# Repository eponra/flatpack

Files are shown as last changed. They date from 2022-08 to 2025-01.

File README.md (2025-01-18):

# flatpack
There is not a lot to unpack. Like... for real.

https://user-images.githubusercontent.com/66600478/183345870-d31b0fc4-497d-4f51-bbe5-db83cf9a2b46.mp4

https://user-images.githubusercontent.com/66600478/183403170-353edabf-4271-400f-9db7-fafc17dc54a0.mp4

https://user-images.githubusercontent.com/66600478/183500945-2cf039b2-9133-45dd-af40-6a08152f20f8.mp4

(flatpack and flathead printing gridfinity parts; flatpack with the old hotendsetup (4010 hotend, 3010 for partcooling)

###### Small Announcement before we go on here:

Mellow has made a fully machined adaptation of flatpack, this machine is called the Mellow M1. Apart from still being able to be folded,
it comes with:
- a new board which is basically a Fly D5 and a Fly Pi Lite v2 married together on the size of the D5 (im very much looking forward
to that board, apart from the cnc'ed adaption of my design is running Flipper ofc; they could do rrf, but we will see)
- a 2.8" touchscreen at the bottom, and a 1.3" touchscreen at the hotend for quick filament changes and quick heating
- a fully cnc'ed frame

- here is the shoplink (no affiliation): https://a.aliexpress.com/_EHAE37a
- There was the idea of doing a kickstarter as every company right now is doing, but mellow ultimately decided against it

https://youtu.be/e8mjv9e-qzc (you see two prototypes here at TCT Asia)  
https://youtu.be/q5g9Ud7NPts?si=8peJaGWEXCFL_qLP&t=52 (starting at the timestamp you see one prototype again)  

Im in no way affiliated with mellow, i dont get anything out of this EXCEPT one of the finished mellow m1. Which im looking very much forward too.

And now lets go on with flatpack here:

###### Technical Data:

- folded volume of roughly 220x210x75mm (so, make sure your spoolbox has these
  inner dimensions at a minimum, as there are some with slightly different dimensions)
- buildvolume of 120x114x114mm, so 1.6 liters
- heated bed that can reach up to 110°C
- Hotend capable of temperatures up to 300°C, if you choose the Copper NF Smart 500°C
- powered through an external (!) powerbrick with 150W, uses 100W max
- the design can theoretically use an AC bed, and consequently a small psu
  enabling everything to fit in one box. 
  For safety reasons I deemed mains wiring to be to dangerous and
  as a result I have selected a DC powered bed to make the build more accessible to the average user.
- Flatpack is fully reprap, meaning that you can print every printable part of flatpack on flatpack.
- now also with Klipper or Octoprint! You need at least the Pi Zero Mount from the files for adding that.
You have also the possibility now to drop the AIO II and just install an SKR Pico along with an Pi Zero (2) W

###### Firmware:

- Marlin configuration is available at [firmware/Marlin](firmware/Marlin). Tested with the AIO II.

###### Some words of caution:

- As you can imagine, a fixed bed cantilever is not optimal for fast speeds or
  larger printvolumes.
- Thankfully, we dont have to deal with a large printvolume. Speed and Acceleration are however a concern here.
Rapid changes in direction can be challenging for any motion system and even more so with this motion system.
As a result consider setting your print speeds and accelerations conservatively.
- So why the fixed bed cantilever? Because it simply looks cool.
- Dual rails are used for load distribution on both the Y and Z axis; these can be a bit
  tricky to align, and can and will cost you a few grey hairs.
- last word of caution: I encourage you to take your time building flatpack, and make certain everything is square, and all the motion system moves smoothly, while everything that should not move is rigid and secure without much play or flexing. 
- its a (functioning) prototype, and will continue to undergo active development and improvements.
- thanks to the user awesomeka001 we now know, that the xz-joiner is indeed printable on flatpack, so flatpack is now full reprap. Meaning if you have one flatpack, you can print all parts of it on that machine.

## This is free for everyone to download and build, or of course to just look at it and take some inspiration or ideas from it. :)

###### ToDo-List
- the XY-joiner is realtively complicated to print and cleanup. One day ill find an easier way to do that.
- flatpack has no spoolholder. The goal is to design a spoolholder, that can travel along in the spoolbox along side the filament you´re carrying with you
- we now have an adapter to fit a Mellow Orbiter Extruder. One day i will make a new carriage for that, so we dont need an adapter, but for now the adapter works well enough, and its still foldable.
- Further optimization of the fanduct/part cooling. I have encountered difficulties designing the fanduct. I have started a repo for ["caterpillar"](https://www.github.com/eponra/caterpillar), which is a partcoolingsolution I designed using CF tubes, which I intend to merge into flatpack eventually.
- the current 3 point-bedmounting is not optimal, as it is simply drilled and tapped M3 threaded holes. I would like to find a better solution down the road.
- you can twist the base and that's not supposed to happen! One solution is to drill through the aluminium extrusions to get screws into the extrusions under the bed. I am convinced there is probably a better solution.

prototyping
(for a break, the latest switch from a totally different hotend/partcooling setup to the actual one. Thats not all steps, just a few)

## Design files

[Fusion 360 Web Flatpack](https://a360.co/3vLUHdm)

This link is sadly viewable only, as I am using the free version of Autodesk
Fusion 360. I also put up a version that only shows parts and positions of the heated inserts. (Attention: the parts inside this are not the most recent, so dont print these.)

[Fusion 360 Web heated inserts](https://a360.co/3tjAQnn)

The link to the latest stable .step file (Ver7) is [here](https://drive.google.com/file/d/1WWorgIL0F1IlGSLJlwn24FICozzornDs/view)
The link to the latest stable Fusion360 file (Ver7) is [here](https://drive.google.com/file/d/1Mac7FewMhGuZk7lCGxoMbQp6idila8Fw/view?usp=drive_link)

###### Changelog:
- from V6 to V7 where changes made to the XZ-joiner, the left Frontmount (so that we can use a shorter front extrusion, this lets us use only 4 300mm 1515 extrusions), i added the screwingholes to the drawing so you know where
to add the extra screws for the base, i added a component which only includes all parts that have inserts + the heated inserts (in a slightly exploded configuration, so you can better see where every insert needs to be), slightly changed
X-Tensioner (just to make one M3-head flush with the print)
- from V4 to V6 there are changes in the X and Y tensioner. Both clamps now feature copper pressfit bushings, and M3 rods. If you started printing already, you only have to watch out for "Y-Tensioner Clamp long v2" and "X-Tensioner Clamp v2".

This is the SKR Pico in front, with the Pi Zero (2) W mount underneath the bed. This is for either Klipper or Octoprint (for Octoprint you can use the AIO II plus the Pi Zero (2) W, and dont need the BTT SKR Pico)


###### A few words of gratitude:

The initial idea of a fixed bed cantilever was not mine, but came from
[apsu](https://github.com/apsu), a constant resident of the
#reprap-and-custombuilds channel in the [3D Printing
discord](https://discord.gg/pQRvDQHk67).  With this i built flathead, the
bigger brother of flatpack, and without [apsu](https://github.com/apsu/) none
of this would have happened.

The initial idea to make this foldable, came from @Ogre.

Also, special thanks to [oliof](https://github.com/oliof/), another extremely
helpful member and Mod of 3D printing, and also a walking dictionary on obscure
3D printing and mechanical knowledge.  And of course, a thank you to everyone
else i forgot from 3D printing and especially the #reprap-and-custombuilds
channel.

Also, everyone nagging me multiple times a day in the super secret
#wheres-flatpack channel...

Flatpack is licensed under [GPL v3.0](/LICENSE).

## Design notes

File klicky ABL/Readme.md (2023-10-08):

## Klicky On Flatpack

#### NOTES
- Since the Z on this printer moves, if you power off the printer at anywhere but Z0, the hotend wont be able to grab the probe  
as it uses it to home Z I havent found a solution yet so let me know if you have any ideas  
- You lose a tiny bit of build volume  

### 1. Printed Parts
 - You need 3 parts for this
 - The **duct**, the standard **probe holder**, and the **probe dock**
 - All 3 parts should be printed in asa or abs as they are near the hotend and bed  
  
    **Duct:**
    - The duct has 3 holes for magnets which you need to press wires into, just the 2 connected to the switch,  
and then you need to trim a hole in the duct for the wires to run out past the fan  
    - Then, you need to run the wires back to the motherboard using the cable sleeving  
    - The duct just mounts like normal with 2 M3 Screws  
    
    **Probe Holder:**
    - The probe holder is just the standard Klicky probe holder 
    - You screw the limit switch in and attach the 3 top magnets 
    - Do not attach the one on the side as its not needed because the probe docks backwards
    
    **Probe Dock:**
    - The probe dock uses 1 magnet and 2 m3 screws
    - It mounts on the 1515 extrusion that has the top y linear rail on it beside the bed
    - It is at X2 Y114 or Y0 (Depending on your setup) roughly
    
### 2. BOM
 What you will need:
 - 4 6x3 Magnets
 - 1 Omron D2F-5
 - 2 STEEL M2 Screws (They need to stick to the dock magnet as the probe is backwards)
 - Wire
 - Super Glue (If necessary)
 - 2 M3x8 Screws 
 - 2 M3 Nuts
 - 1 Heated Insert for Duct
 
 ### 3. Assembly
  - Assemble the Klicky probe by putting the 3 magnets in the top and screwing the limit switch in
  - Insert the 3 Magnets into the duct along with 2 wires on the left and right magnets so the switch can work (I recommend testing continuity with them)
  - Trim a small hole in the end of the duct to allow the wires to come out, on the right side of the fan
  - Route the wires to the motherboard and attach them to z stop or a probe pin (I use z stop)
  - Attach the one magnet into the probe dock and use the 2 M3 screws and nuts to attach it to the 1515 extrusion that is where the y belt tensioner is
  - Move flatpack manually until you find the coordinates of the klicky probe, Mark them down (For me they are Z12.62 Y6 X2)
  **Thats It!! Assembly for Klicky is done**
  
  ### 4. Firmware
Instructions based on Marlin 2.1.2.1
    If you are using Klipper, there are guides online  
    Used this as a reference https://www.youtube.com/watch?v=egWpvaTsl10  
    ### - **Configuration.h**  
          - Uncomment #define Z_MIN_PROBE_USES_Z_MIN_ENDSTOP_PIN  
          - Uncomment #define FIX_MOUNTED_PROBE  
          - Uncomment #define NOZZLE_TO_PROBE_OFFSET { 21.4, -11.4, -10.75} (Those are my offset values in order of XYZ)  
          - Set #define PROBING_MARGIN to 15  
          - Set #define Z_CLEARANCE_DEPLOY_PROBE 0 and #define Z_CLEARANCE_BETWEEN_PROBES 5  
          - Make sure #define Z_PROBE_LOW_POINT is set to -5   
          - Uncomment #define RESTORE_LEVELING_AFTER_G28  
          - Uncomment #define LCD_BED_LEVELING  
          - Uncomment #define Z_SAFE_HOMING  
          - Uncomment #define AUTO_BED_LEVELING_BILINEAR  
          - If you want, you can uncomment this to test your mesh #define G26_MESH_VALIDATION  
          - Set  #define GRID_MAX_POINTS_X to 5  
    ### - **Configuration_adv.h**  
          - These are all your macros for abl, you may have to change the values depending on where your mount is  

#### Here are my custom macros:   

> ; Macros
> ; M810 Home XY  and deploy probe
> M810 G28 XY|G1 Z12.62|G1 X2|G1 Y11 F2400|G1 X2 Y6 Z12.62 F1200|G1 Y25 Z12.62 F2400
>
> ; M811 Home XYZ and stow probe
> M811 G28 XYZ|G1 Z12.62|G1 X2|G1 Y11 F2400|G1 X2 Y6 Z12.62 F1200|G1 X50 Y6 Z12.62 F2400
> 
> ; M812 Stow probe without homing
> M812 |G1 Z12.62|G1 X2|G1 Y11 F2400|G1 X2 Y6 Z12.62 F1200|G1 X50 Y6 Z12.62 F2400
> 
> M117 Macros Loaded

- Uncomment #define STARTUP_COMMANDS and put your macros like this (in one line, seperated by \n and in quotes)
**"M810 G28 XY|G1 Z12.62|G1 X2|G1 Y11 F2400|G1 X2 Y6 Z12.62 F1200|G1 Y25 Z12.62 F2400**
>    \nM811 G28 XYZ|G1 Z12.62|G1 X2|G1 Y11 F2400|G1 X2 Y6 Z12.62 F1200|G1 X50 Y6 Z12.62 F2400  
>    \nM812 |G1 Z12.62|G1 X2|G1 Y11 F2400|G1 X2 Y6 Z12.62 F1200|G1 X50 Y6 Z12.62 F2400"  
   - Uncomment #define GCODE_MACROS
   - Set #define GCODE_MACROS_SLOT_SIZE to 150
   - Uncomment #define CUSTOM_MENU_MAIN 
   
## These are my menu Items :
> // Custom Menu: Main Menu  
> #define CUSTOM_MENU_MAIN  
> #if ENABLED(CUSTOM_MENU_MAIN)  
> #define CUSTOM_MENU_MAIN_TITLE "Klicky Probe"  
> //#define CUSTOM_MENU_MAIN_SCRIPT_DONE ""  
> #define CUSTOM_MENU_MAIN_SCRIPT_AUDIBLE_FEEDBACK  
> //#define CUSTOM_MENU_MAIN_SCRIPT_RETURN   // Return to status screen after a script  
> #define CUSTOM_MENU_MAIN_ONLY_IDLE         // Only show custom menu when the machine is idle  
>  
> #define MAIN_MENU_ITEM_1_DESC "Deploy Probe"  
> #define MAIN_MENU_ITEM_1_GCODE "M810"  
> //#define MAIN_MENU_ITEM_1_CONFIRM          // Show a confirmation dialog before this action  
>  
> #define MAIN_MENU_ITEM_2_DESC "Stow Probe"  
> #define MAIN_MENU_ITEM_2_GCODE "M811"  
>  //#define MAIN_MENU_ITEM_2_CONFIRM  
>  
> #define MAIN_MENU_ITEM_3_DESC "Stow Probe Without Homing"  
> #define MAIN_MENU_ITEM_3_GCODE "M812"  
> //#define MAIN_MENU_ITEM_3_CONFIRM  
>  
> #define MAIN_MENU_ITEM_4_DESC "Deploy and Home"  
> #define MAIN_MENU_ITEM_4_GCODE "M810\nG28 Z"  
> //#define MAIN_MENU_ITEM_4_CONFIRM  
> 
> #define MAIN_MENU_ITEM_5_DESC "Deploy and Probe Bed"  
> #define MAIN_MENU_ITEM_5_GCODE "M810\nG28 Z\nG29"  
> //#define MAIN_MENU_ITEM_5_CONFIRM  
> #endif  
        
   - You can also use an sd card to run the commands on startup, but I like to use eeprom to store them  
   - I'd reccomend watching teaching techs video on this, as it goes into more detail  
        
  ## Thats all! You can now put these commands in your start gcode and it will probe automatically  
   Message me if you have any questions :)   

Start Gcode:   

M810
G28
G29
M812
G1 Z+30 F1500
G1 Z15.0 F6000 ;Move the platform down 15mm
G92 E0

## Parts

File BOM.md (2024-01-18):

# Bill of Materials
(I´ve linked mostly black anodized parts. You can ofc source your own in the colour you want.)

- [ ]  **Head**
  - FYSETC AIO II
  - 45,30€
  - https://www.aliexpress.com/item/32331322896.html
  - (you can now also go BTT SKR Pico + Pi Zero (2) W (then you dont need the AIO II), OR only + Pi Zero (2) W WITH the AIO II, for using Klipper)

- [ ]  **Extruder**
  - Mellow Sherpa Mini, 63,14€
  - https://www.aliexpress.com/item/1005003671542821.html
  - or Mellow Orbiter (needs testing)

- [ ]  **Hotend**
  - Mellow NF Smart
  - 35,77€
  - https://www.aliexpress.com/item/4000804638258.html
  - there are many more compatible; max overall length is 50mm, the actual mounts needs a Hotend that uses the 2xM3 mounting option without changes. May need adjustments on the fanduct though.

- [ ]  **Heatbed**
  - 150x150x3mm aluminium plate
  - 8€ from ebay
  - 24V 120x120 silicone heater
  - 22,24€ 
  - https://www.aliexpress.com/item/1005001815326438.html
  - 3x Springs 8x4x20mm
  - 1,56€
  - https://www.aliexpress.com/item/1005001839105857.html

- [ ]  **PSU**
  - external 24V powerbrick without active cooling
  - 28,11€
  - https://www.aliexpress.com/item/1005001303610253.html

- [ ]  **Rails**
  - 5x MGN9C in 150mm black anodized
  - 50€
  - https://www.robotdigg.com/product/1314/Black-anodized-linear-rail-7,-9,-12-and-15

- [ ]  **Hotend Fan**
  - 24V 3010 blower
  - 10,22€
  - https://www.aliexpress.com/item/1005003059620933.html

- [ ]  **Part Cooling Fan**
  - 24V gdstime 4020 blower
  - 11,84€
  - https://www.aliexpress.com/item/1005001436999999.html
  - again two

- [ ]  **Leadscrew**
  - T8, black, 250mm
  - 10,97€
  - https://www.aliexpress.com/item/1005002054258631.html
  - you have to cut that leadscrew(!) to length

- [ ]  **5 to 8mm Coupler**
  - A Set of 5mm to 8mm Coupler, for the Leadscrew
  - 10,97€
  - https://www.aliexpress.com/item/32368507972.html

- [ ]  **Stepper Motors**
  - 3pc Set Nema 17
  - 24,31€
  - https://www.aliexpress.com/item/1005001650755939.html

- [ ]  **Extrusions**
  - 4x 300mm 1515, black anodized,
  - 13,03€
  - https://www.makerbeam.com/300mm-4p-black-makerbeamxl-15mmx15mm.html
  - must also be cut to length (1st 300mm 165mm&128mm, 2nd 300mm 165mm&108mm, 3rd 300mm 177mm&106mm, 4th 300mm 160mm&82mm)

- [ ]  **M3 Heated Inserts**
  - a lot (pls choose M3 X D4.6 X L3.0; longer is possible, but L3.0 is needed for Orbiter V2 Extruder)
  - 6,50€
  - https://www.aliexpress.com/item/4000232858343.html
  - you get 100pcs

- [ ]  **M3 Screws** 
  - 22,19€ for a non-black set
  - https://www.aliexpress.com/item/1005004145730693.html
  - 440pcs in the set, only M3. If you source your own set, remember you need at least two M3 in 40mm.

- [ ]  **2x 110mm closed loop gt2 belt 6mm** 
  - 1,54€ for two
  - https://www.aliexpress.com/item/4000936363508.html

- [ ]  **80cm gt2 belt 6mm** 
  - 7,54€ for 2m
  - https://www.aliexpress.com/item/32952396111.html

- [ ]  **roughly 25 M3 Nuts as tnuts** 
  - no cost, because there are more already in the M3 Screw Set
  - i experimented with tnut-style variants for the build in 1515, but M3 nuts work well, so no reason to buy them
  - roughly 25, because its on you how many you use for the rails

- [ ]  **4x F695 2RS Bearings** 
  - 5,69€ for 10
  - https://www.aliexpress.com/item/32850989216.html

- [ ]  **2x smooth Idler** 
  - 2,22€ for two
  - https://www.aliexpress.com/item/33060233087.html (from this link its the "type 4", and dont forget to choose either black or silver)
  - important here is that the pully has a 3mm inner diameter hole, and is 8mm tall, and the flange has a diameter of 13mm (if you want to source it yourself)

- [ ]  **6x Pulley 16T GT2 6mm** 
  - 12,42€ for six
  - https://www.aliexpress.com/item/1005004568068197.html
  - important is here that the pully has a 5mm inner diameter hole, is 14mm tall, and has 16 teeth (if you want to source it yourself)

- [ ]  **3x Endstops** 
  - 0,84€ for 5
  - https://www.aliexpress.com/item/4000434289043.html

- [ ]  **4x copper bushings, 3*5*2.1/7*0.6mm** 
  - 1,92€ for 5
  - https://www.aliexpress.com/item/1005005065448057.html
  - bushings you press into the x- and y-tensioner, to then push a 3mm rod through

- [ ]  **2x 3mm steel rod, 100mm long** 
  - 1,54€ for 2 x 100mm
  - https://www.aliexpress.com/item/32427862310.html
  - 3mm rod you will have to cut to size

- [ ]  **1x 5mm steel rod, 100mm long** 
  - 1,75€ for 1 x 100mm
  - https://www.aliexpress.com/item/32427862310.html
  - 5mm rod you will have to cut to size

- [ ]  **4x Rubber Feet** 
  - its not really important which one you choose, but they have to be 10mm in height, and can be up to 23mm in width
  - you can ofc simply design your own foot, or cut something to size that fit the existing feet, and add the 10mm in height

- [ ]  **Optional: for the tool mount you will need** 
  - a 6x2mm neodym magnet
  - another m3 nut and screw
  - a 2.5mm allen key
  - a nozzle spanner, they´re mostly all the same, i link here the twotrees one
  - https://www.aliexpress.com/item/4000601733774.html

**All-in-all that's 388,30€. All that is without postage or customs, so this
price could still fluctuate a tad.**

Also, you could maybe save a few bucks left and right. It doesnt have to be
gdstime fans for example, and a 120W PSU will also do the job.  With that out
of the way, happy sourcing and building!

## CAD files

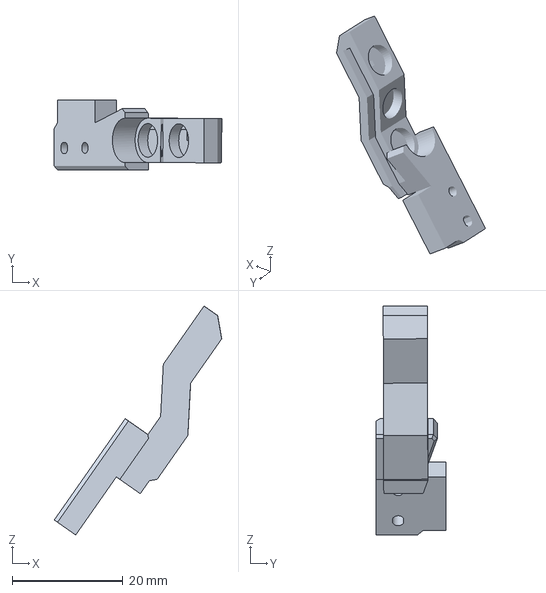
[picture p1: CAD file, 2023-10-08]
manualklicky/manualklicky-main.3mf
30.2 x 12.6 x 41.3 mm

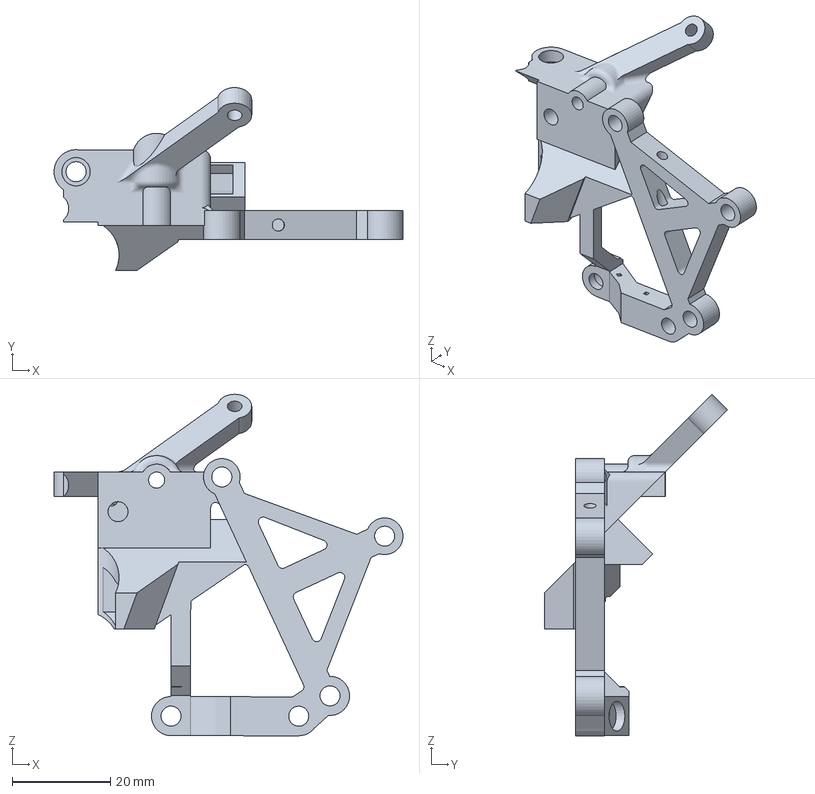
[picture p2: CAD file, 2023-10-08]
manualklicky/manualklicky-hotendfan+partcoolingassembly v3.3mf
71.2 x 37.3 x 69.7 mm

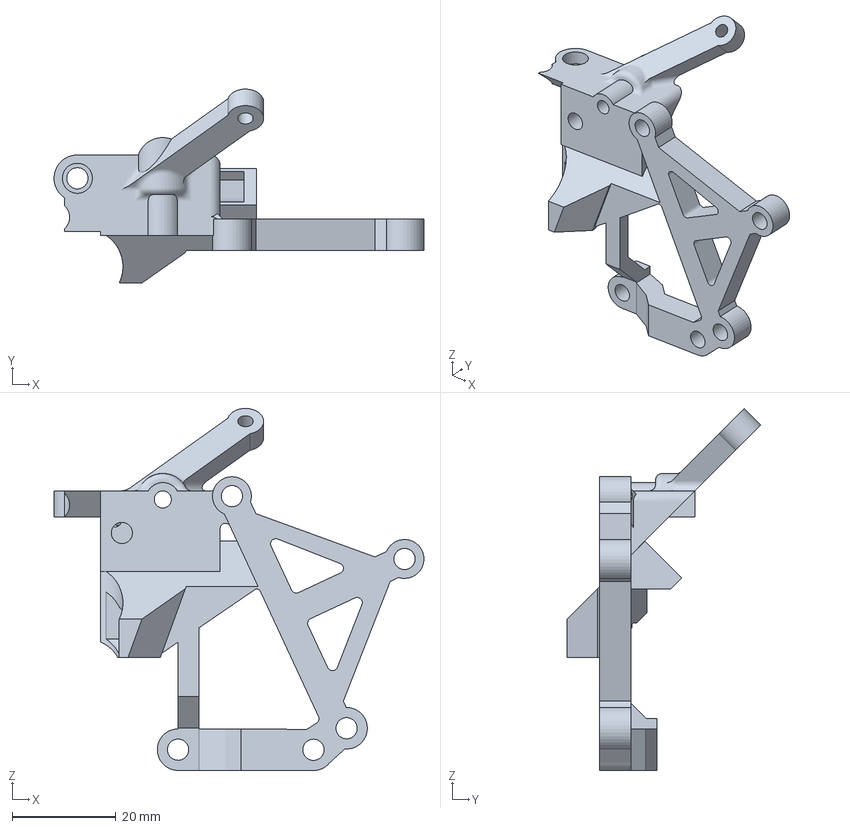
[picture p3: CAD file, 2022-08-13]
3mf/hotendfan+partcoolingassembly v3.3mf
71.2 x 37.3 x 69.7 mm

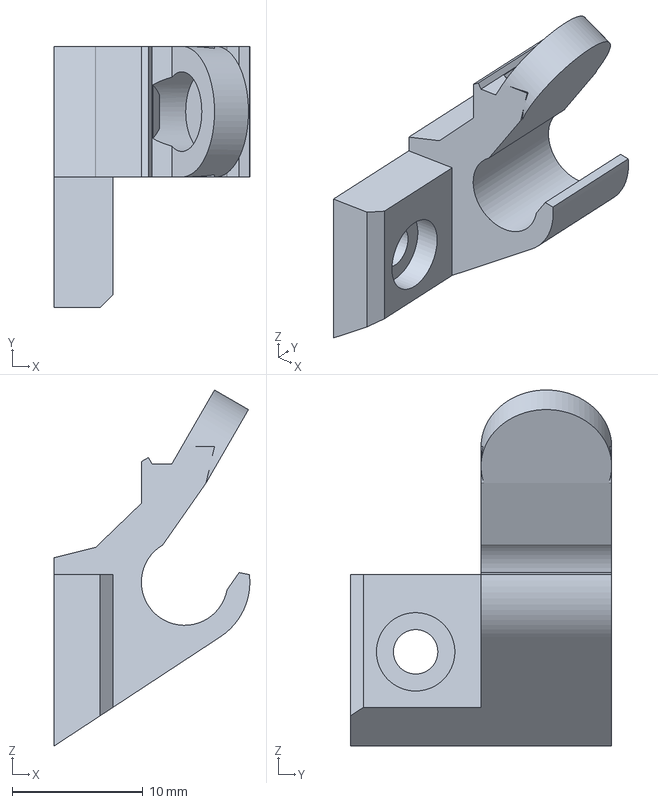
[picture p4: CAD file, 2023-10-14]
3mf/tools_mount.3mf
15.0 x 20.0 x 27.2 mm

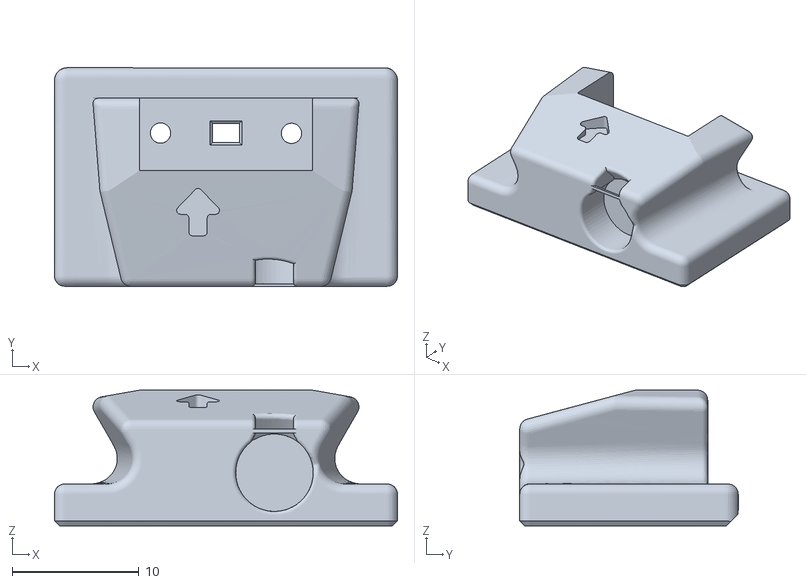
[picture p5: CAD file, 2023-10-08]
klicky ABL/KlickyProbe_v2.stl
27.0 x 17.2 x 10.7

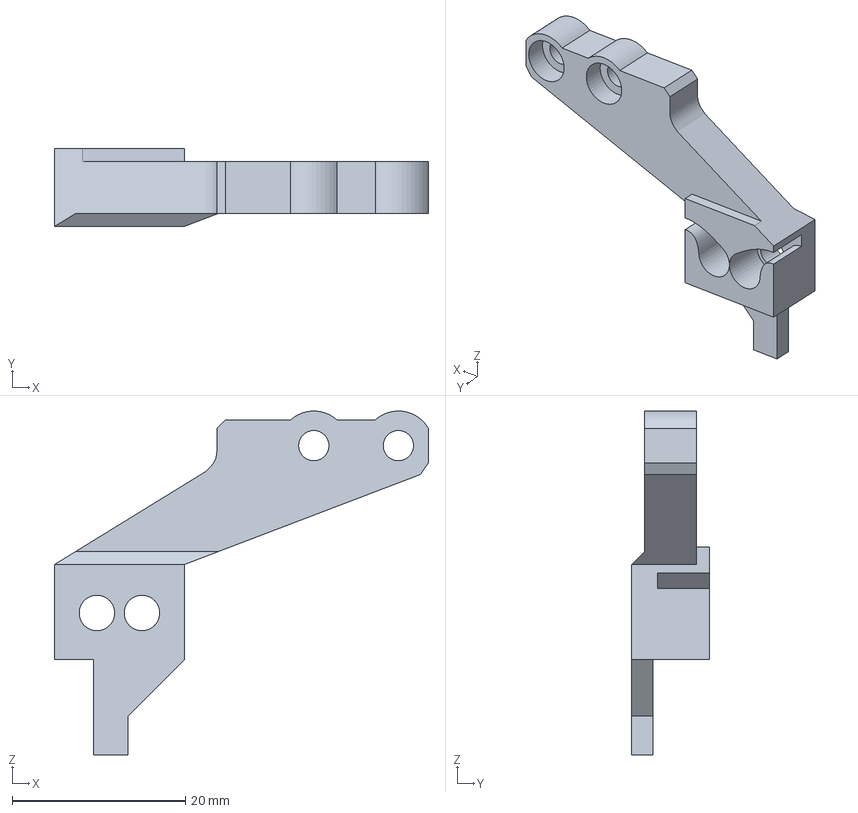
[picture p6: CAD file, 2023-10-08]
3mf/rail-to-x-adapter v5.3mf
43.2 x 9.00 x 39.7 mm

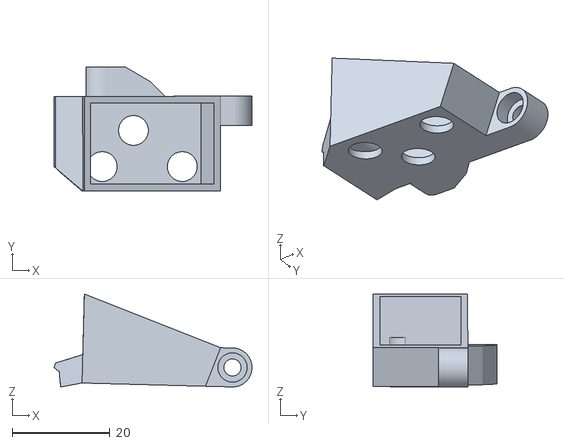
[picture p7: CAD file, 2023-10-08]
klicky ABL/fanshroud_v5_normal_Klicky.stl
40.6 x 25.4 x 19.1

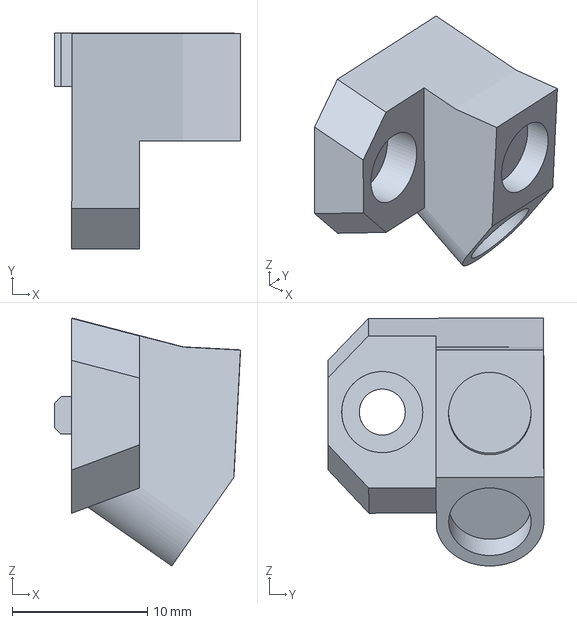
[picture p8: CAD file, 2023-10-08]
manualklicky/manualklicky-mount.3mf
13.8 x 16.0 x 18.3 mm

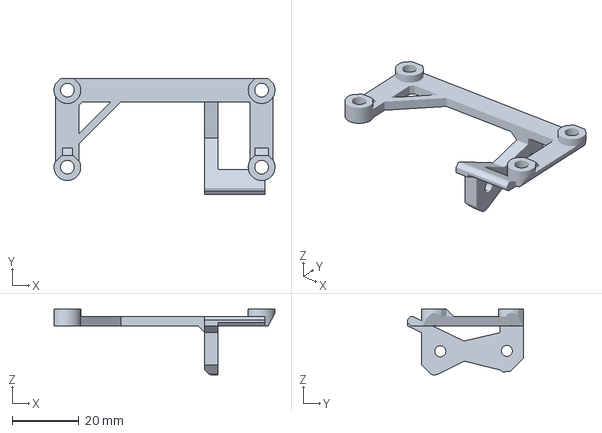
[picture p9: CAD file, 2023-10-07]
3mf/Pi Zero W mount AIO II and SKR Pico.3mf
66.0 x 34.7 x 19.7 mm

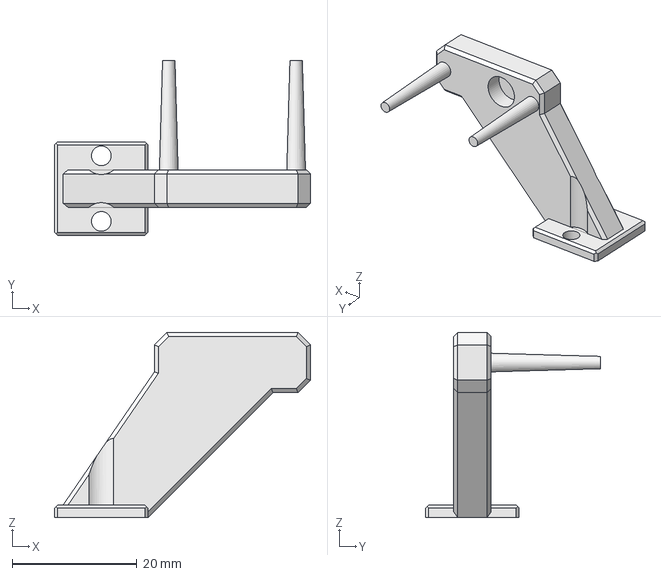
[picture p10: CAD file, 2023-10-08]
klicky ABL/Probe_Dock_For_Flatpack.FCStd
41.0 x 28.0 x 29.6 mm

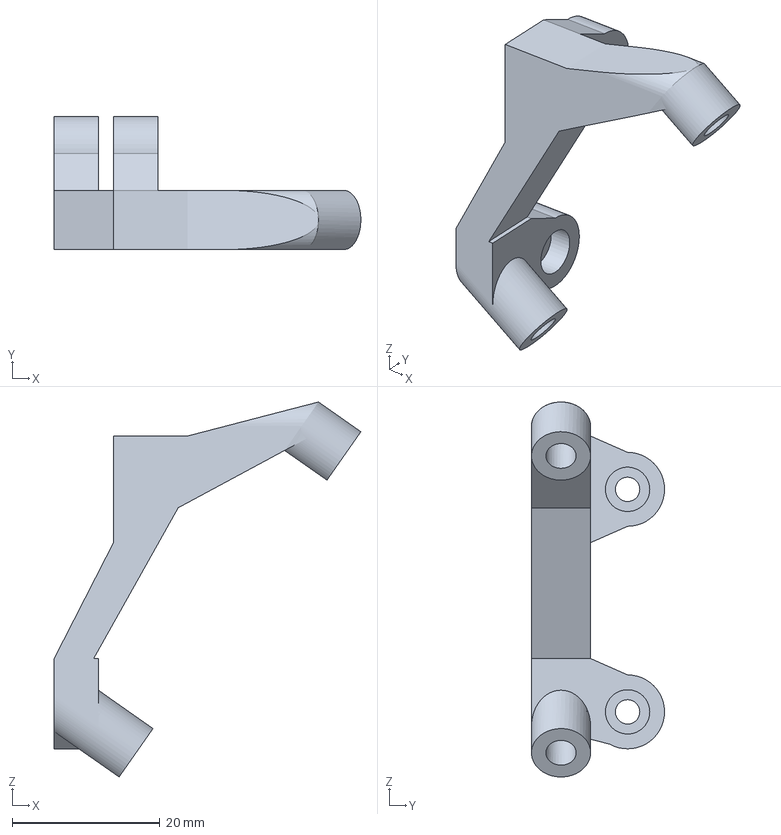
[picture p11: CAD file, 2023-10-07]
3mf/SKR Pico Mount Right.3mf
41.5 x 18.0 x 50.7 mm

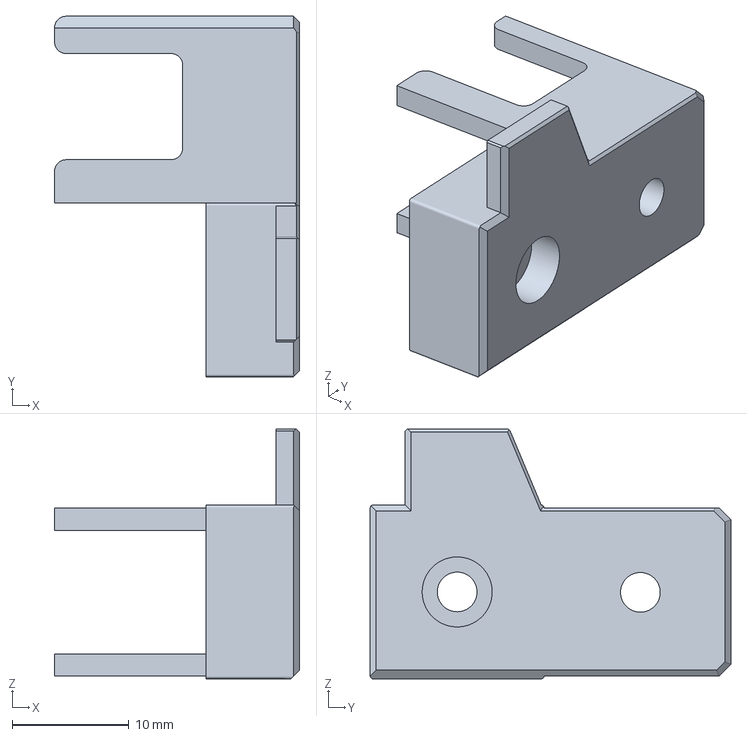
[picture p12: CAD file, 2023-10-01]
3mf/X-Tensioner v3.3mf
21.0 x 30.9 x 21.4 mm

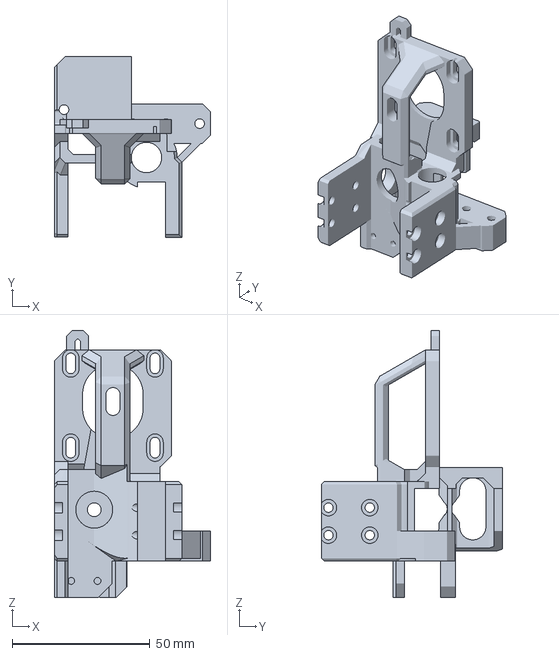
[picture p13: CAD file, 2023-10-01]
3mf/XZ-joiner v4.3mf
56.8 x 65.7 x 97.0 mm

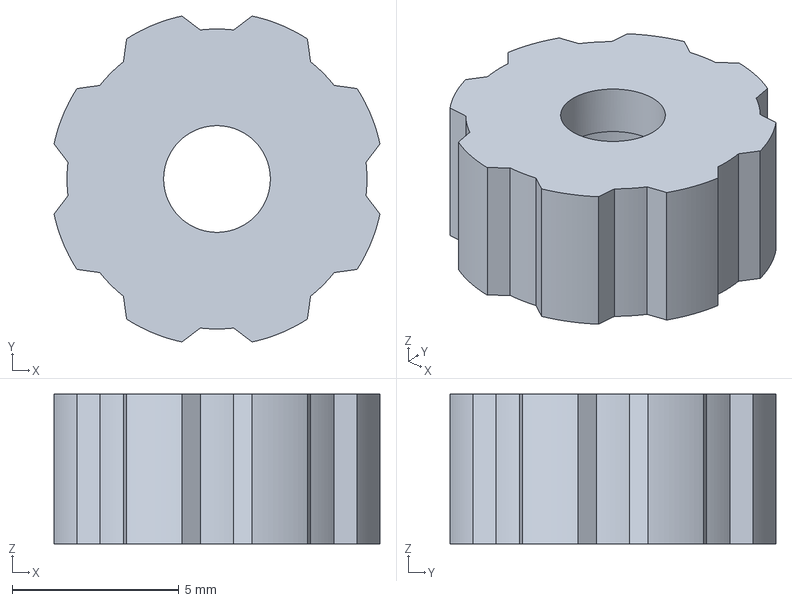
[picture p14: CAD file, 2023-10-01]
3mf/Endstopwheel Z v2.3mf
9.78 x 9.78 x 4.50 mm

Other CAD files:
3mf/SKR Pico Mount Left.3mf
3mf/Frontmount L v3.3mf
3mf/fanshroud v5 normal.3mf
3mf/Motormount Y sidebracket.3mf
3mf/Endstopmount Y.3mf
3mf/Endstopwheel Z.3mf
3mf/Frontmount R v2.3mf
3mf/LCD-mount L v2.3mf
3mf/LCD-mount R v2.3mf
3mf/Motormount Y v4.3mf
3mf/X-Tensioner Clamp v2.3mf
3mf/X-Tensioner v2.3mf
3mf/XT60_mount.3mf
3mf/XZ-joiner v3.3mf
3mf/Y-Motor-Towermount v4.3mf
3mf/Y-Motor-Towermount-Base.3mf
3mf/Y-Tensioner Clamp long v2.3mf
3mf/Y-Tensioner.3mf
3mf/foot v2.3mf
3mf/hotend_extruder_mount.3mf
3mf/rail-to-Z-adapter v4.3mf
klicky ABL/Probe_Dock_For_Flatpack.stl

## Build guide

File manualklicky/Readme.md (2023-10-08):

## manualklicky for Flatpack

**manualklicky** for Flatpack is a project i designed, to NOT lose any space in the already small buildvolume of flatpack.  
Problem being of course, that this has a manual component; it is still technically ABL though.  
(ABL = automated bed leveling)  
The idea was of course 100% influenced by Klicky, but shares no parts with it. (because it wont fit. ;) )  
THIS IS STILL A WIP !!! THE PART MISSING IS ADDING THE PROBE TO THE FIRMWARE !!!
  
### Description:  
- on the proper klicky you have to move your printhead outside your buildvolume to get to the klickyprobe  
- on flatpack, we use every mm of our buildvolume, and i decided to not give that away for a ABL probe  
- so, you can start the ABL-probing, but have to remember to add the probe before you do that, AND have to remember to take it off after probing  
- the idea behind klicky is that the magnets job is not only to connect the probe in place, but to also provide the electric connection for the actual probe. This is ofc here exactly the same.
#### Note:  
- if you dislike any manual interaction for ABL-probing, you can use **Klicky for flatpack**,which Awesomeka designed and provided for the GitHub, and which you find here under the folder with the same name   
  
### 1. Printed Parts  
- you need to switch out one part, and print two new parts  
- the part you have to switch out, is the **hotendfan+partcoolingassembly vx.3mf"** for the variant with "manualklicky-" in front  
- apart from that you have to print two new parts: **manualklicky-mount.3mf", which is the magnetic mount or dock, you have to install on the front of the printer, and  
**manualklicky-main.3mf**, which is the part that holds the actual probe  

### 2. BOM  
You need:  
- 7x 6x2 neodym magnets  
- 4x heated inserts in M3 (M3 X D4.6 X L3.0 is ideal, just like on the main BOM), all needed for the **hotendfan+partcoolingassembly** part you switch out  
- 1x Omron D2F-5 (or any other microswitch that has the same measurements)  
- wires ofc  
- glue for glueing the magnets to the plastic. I also like to give the cables a dot or two so they stay where they are  
- 1x M3x5 or M3x6 screw  
- 1x M3 T-Nut for 1515, OR 1x M3 Nut  
- a roughly 2mm thick self-adhesive feltpad; this is used for gliding along the x-axis and making sure the probe transfer all forces to the x-extrusion on every probing

### 3. Assembly
- if you have already printed the **hotendfan+partcoolingassembly.3mf**, you need to reprint the "manualklicky-" version, and add the heated inserts to that
- after you have done that, you want to add 3 6x2mm neodym magnets, maybe with glue if that doesnt hold well
- two of the 6x2 magnets need you to add wire to the back, you know which by the channels in the back
- print the **manualklicky-main.3mf**, screw the omron microswitch to it, and add the magnets. Again, for two of the three magnets you need to connect wire to the magnets
- the Probe has a mount designed to be docked/mounted on the front right. Print that, put the magnets in, and simply screw it onto the front top extrusion. The probe is hold  
in place there by magnets, just like on the head.

### 4. Instructions
- i dont have any instructions on how to add this to Marlin or Klipper yet. 

### Screenshots
  
  
  
  


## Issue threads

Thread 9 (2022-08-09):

Add missing parts to BOM

eponra, 2022-08-09:
The BOM is missing the belts (closed and open) and tnuts used.

IDKhowtousethissiteLol, 2022-08-09:
Idlers, Pulleys, Endstops

eponra, 2022-08-10:
Added missing parts to BOM, but still two parts missing. Will add them later, so i keep this issue open until resolved.

eponra, 2022-08-10:
Added missing parts to BOM, slightly changed the setup for x and y-tensioner, am now re-uploading the fusion and step-files.

Closed 2022-08-10.

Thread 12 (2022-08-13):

Missing items on BOM

lildevilx, 2022-08-13:
Hello,

I was going through the BOM and cross referencing parts with the drawing and noticed that you have missed a leadscrew coupler for the Z axis. I'm assuming something like this?
https://www.aliexpress.com/item/33031786581.html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
Also, is there any reason why you didn't opt for integrated lead screw motors? or is it just purely cost?

Since you're using the TMC2208 version of the AIO board, is there any reason why you didn't use sensorless homing?

Might be nice to add a flex plate bed into the BOM as well.

I'm quite interested in building one of these and use when I'm traveling for work, hoping to see more improvements!

eponra, 2022-08-13:
Hello there!

I missed the coupler, thanks for pointing that out. Will add that right away.
Also, its exactly the one from your link.

To the rest of your questions:
- integrated lead screw vs not integrated is not really a question of price. I like to be able to switch out motors, also i wanted a black leadscrew
- sensorless homing (so StallGuard) is not available on TMC2208 drivers
- i only add things to the BOM, which you really need for operation. Flexplate is an addon that will also cost some mm in Z

You can ofc add what you you want :)

Closed 2022-08-13.

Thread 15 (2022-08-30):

24v part cooling

lildevilx, 2022-08-30:
FYI, the link for the part cooling fan brings you to the 12v version instead of the 24v.
Feel free to ask me when I found out :P

eponra, 2022-08-30:
Hey there!
I just followed that link out of the BOM, and asked others to follow the same link, and it definitely lead to the 24V version.
(its stated in the name, and in the picture it also shows 24V, and you cant choose anything else)

Either the link gets corrupted on aliexpress , and leads you to the wrong fan, or they sent you the wrong one?

lildevilx, 2022-08-30:
Sorry, part hotend fan, not the part cooling.

- Exhaust Cooler Radiator Blower Fan

eponra, 2022-08-30:
Ah! Checked it, and you´re right, that linked to a 12V version of the 3010 hotend fan you need.
Fixed it as of now!
Sorry for the inconvience!

Closed 2022-08-30.

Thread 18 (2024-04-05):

Array of fixed bed cantilever printers

ukdavewood, 2024-04-05:
I am working on a concept of joining together cheap cantilever printers to form an array. With the intention as a) doing efficient multi colour printing, and b) Parallel printing.

What I am intending to do first is to build a couple of fixed bed cantilever prototypes out of existing old printers -  I came across your design - and I think I will have a go a creating a couple of your flatpack printers joined together on their Y rails - with linear rails spanning the whole length.

I guess the biggest challenge will be working out the belting system to drive multiple multiple cantilevers down the same axis.
My initial thought was to have the Y motor on the cantilever too and only have one belt or some sort of gear rack to run the cantilevers along - but I guess that will add even more weight - so might see if there is a way to fit several parallel belts between the two extrusions.

I have created this video with some animations in it to explain the concept - and looking at your step file I think I can fairly easily add it in. - So will probably release a further version in the next few days.

https://youtu.be/pKFV6oJn1yQ?si=lu9xP3r-Mgsi_Ihq

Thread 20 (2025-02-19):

UK

gurmukhp, 2025-02-19:
This is an excellent project.

I'm in the UK and having a hard time sourcing the parts, some of the AliExpress links no longer work. Do you know of anyone that has made your printer in the UK? Would love to see how it looks.

Thanks

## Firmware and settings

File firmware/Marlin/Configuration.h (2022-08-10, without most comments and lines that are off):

#pragma once
#define CONFIGURATION_H_VERSION 020000
#define STRING_CONFIG_H_AUTHOR "(none, default config)" // Who made the changes.
#define SHOW_BOOTSCREEN
#define SERIAL_PORT 1 // libmaple 0 for USB ,1 for serial
#define BAUDRATE 115200
  #define MOTHERBOARD BOARD_FYSETC_AIO_II
#define CUSTOM_MACHINE_NAME "FlatPack"
#define EXTRUDERS 1
#define DEFAULT_NOMINAL_FILAMENT_DIA 1.75
#define TEMP_SENSOR_0 1
#define TEMP_SENSOR_1 0
#define TEMP_SENSOR_2 0
#define TEMP_SENSOR_3 0
#define TEMP_SENSOR_4 0
#define TEMP_SENSOR_5 0
#define TEMP_SENSOR_BED 1
#define TEMP_SENSOR_CHAMBER 0
#define DUMMY_THERMISTOR_998_VALUE 25
#define DUMMY_THERMISTOR_999_VALUE 100
#define MAX_REDUNDANT_TEMP_SENSOR_DIFF 10
#define TEMP_RESIDENCY_TIME     10  // (seconds) Time to wait for hotend to "settle" in M109
#define TEMP_WINDOW              1  // (°C) Temperature proximity for the "temperature reached" timer
#define TEMP_HYSTERESIS          3  // (°C) Temperature proximity considered "close enough" to the target
#define TEMP_BED_RESIDENCY_TIME 10  // (seconds) Time to wait for bed to "settle" in M190
#define TEMP_BED_WINDOW          1  // (°C) Temperature proximity for the "temperature reached" timer
#define TEMP_BED_HYSTERESIS      3  // (°C) Temperature proximity considered "close enough" to the target
#define HEATER_0_MINTEMP   5
#define HEATER_1_MINTEMP   5
#define HEATER_2_MINTEMP   5
#define HEATER_3_MINTEMP   5
#define HEATER_4_MINTEMP   5
#define HEATER_5_MINTEMP   5
#define BED_MINTEMP        5
#define HEATER_0_MAXTEMP 275
#define HEATER_1_MAXTEMP 275
#define HEATER_2_MAXTEMP 275
#define HEATER_3_MAXTEMP 275
#define HEATER_4_MAXTEMP 275
#define HEATER_5_MAXTEMP 275
#define BED_MAXTEMP      100
#define PIDTEMP
#define BANG_MAX 255     // Limits current to nozzle while in bang-bang mode; 255=full current
#define PID_MAX BANG_MAX // Limits current to nozzle while PID is active (see PID_FUNCTIONAL_RANGE below); 255=full current
#define PID_K1 0.95      // Smoothing factor within any PID loop
  #define PID_EDIT_MENU         // Add PID editing to the "Advanced Settings" menu. (~700 bytes of PROGMEM)
  #define PID_AUTOTUNE_MENU     // Add PID auto-tuning to the "Advanced Settings" menu. (~250 bytes of PROGMEM)
  #define PID_FUNCTIONAL_RANGE 10 // If the temperature difference between the target temperature and the actual temperature
  #define  DEFAULT_Kp 11.71
  #define  DEFAULT_Ki 0.57
  #define  DEFAULT_Kd 59.60
#define PIDTEMPBED
#define MAX_BED_POWER 255 // limits duty cycle to bed; 255=full current
  #define MIN_BED_POWER 0
  #define DEFAULT_bedKp 41.04
  #define DEFAULT_bedKi 2.22
  #define DEFAULT_bedKd 506.63
#define PREVENT_COLD_EXTRUSION
#define EXTRUDE_MINTEMP 17
#define PREVENT_LENGTHY_EXTRUDE
#define EXTRUDE_MAXLENGTH 200
#define THERMAL_PROTECTION_HOTENDS // Enable thermal protection for all extruders
#define THERMAL_PROTECTION_BED     // Enable thermal protection for the heated bed
#define THERMAL_PROTECTION_CHAMBER // Enable thermal protection for the heated chamber
#define USE_XMIN_PLUG
#define USE_YMIN_PLUG
#define USE_ZMIN_PLUG
#define ENDSTOPPULLUPS
#define X_MIN_ENDSTOP_INVERTING false // Set to true to invert the logic of the endstop.
#define Y_MIN_ENDSTOP_INVERTING false // Set to true to invert the logic of the endstop.
#define Z_MIN_ENDSTOP_INVERTING false // Set to true to invert the logic of the endstop.
#define X_MAX_ENDSTOP_INVERTING false // Set to true to invert the logic of the endstop.
#define Y_MAX_ENDSTOP_INVERTING false // Set to true to invert the logic of the endstop.
#define Z_MAX_ENDSTOP_INVERTING false // Set to true to invert the logic of the endstop.
#define Z_MIN_PROBE_ENDSTOP_INVERTING false // Set to true to invert the logic of the probe.
#define X_DRIVER_TYPE  TMC2208
#define Y_DRIVER_TYPE  TMC2208
#define Z_DRIVER_TYPE  TMC2208
#define E0_DRIVER_TYPE TMC2208
#define DEFAULT_AXIS_STEPS_PER_UNIT   { 99.34, 100, 1600, 668.30 }
#define DEFAULT_MAX_FEEDRATE          { 100, 100, 100, 100 }
#define DEFAULT_MAX_ACCELERATION      { 250, 250 , 100, 300 }
#define DEFAULT_ACCELERATION          1000    // X, Y, Z and E acceleration for printing moves
#define DEFAULT_RETRACT_ACCELERATION  3000    // E acceleration for retracts
#define DEFAULT_TRAVEL_ACCELERATION   800    // X, Y, Z acceleration for travel (non printing) moves
  #define DEFAULT_XJERK 10.0
  #define DEFAULT_YJERK 10.0
  #define DEFAULT_ZJERK  0.3
#define DEFAULT_EJERK    5.0  // May be used by Linear Advance
#define Z_MIN_PROBE_USES_Z_MIN_ENDSTOP_PIN
#define X_PROBE_OFFSET_FROM_EXTRUDER 10  // X offset: -left  +right  [of the nozzle]
#define Y_PROBE_OFFSET_FROM_EXTRUDER 10  // Y offset: -front +behind [the nozzle]
#define Z_PROBE_OFFSET_FROM_EXTRUDER 0   // Z offset: -below +above  [the nozzle]
#define MIN_PROBE_EDGE 10
#define XY_PROBE_SPEED 8000
#define Z_PROBE_SPEED_FAST HOMING_FEEDRATE_Z
#define Z_PROBE_SPEED_SLOW (Z_PROBE_SPEED_FAST / 2)
#define Z_CLEARANCE_DEPLOY_PROBE   10 // Z Clearance for Deploy/Stow
#define Z_CLEARANCE_BETWEEN_PROBES  5 // Z Clearance between probe points
#define Z_CLEARANCE_MULTI_PROBE     5 // Z Clearance between multiple probes
#define Z_PROBE_LOW_POINT          -2 // Farthest distance below the trigger-point to go before stopping
#define Z_PROBE_OFFSET_RANGE_MIN -20
#define Z_PROBE_OFFSET_RANGE_MAX 20
#define X_ENABLE_ON 0
#define Y_ENABLE_ON 0
#define Z_ENABLE_ON 0
#define E_ENABLE_ON 0 // For all extruders
#define DISABLE_X false
#define DISABLE_Y false
#define DISABLE_Z false
#define DISABLE_E false             // For all extruders
#define DISABLE_INACTIVE_EXTRUDER   // Keep only the active extruder enabled
#define INVERT_X_DIR true
#define INVERT_Y_DIR true
#define INVERT_Z_DIR false
#define INVERT_E0_DIR true
#define INVERT_E1_DIR false
#define INVERT_E2_DIR false
#define INVERT_E3_DIR false
#define INVERT_E4_DIR false
#define INVERT_E5_DIR false
#define X_HOME_DIR -1
#define Y_HOME_DIR -1
#define Z_HOME_DIR -1
#define X_BED_SIZE 120
#define Y_BED_SIZE 114
#define X_MIN_POS 0
#define Y_MIN_POS 0
#define Z_MIN_POS 0
#define X_MAX_POS X_BED_SIZE
#define Y_MAX_POS Y_BED_SIZE
#define Z_MAX_POS 114
#define MIN_SOFTWARE_ENDSTOPS
  #define MIN_SOFTWARE_ENDSTOP_X
  #define MIN_SOFTWARE_ENDSTOP_Y
  #define MIN_SOFTWARE_ENDSTOP_Z
#define MAX_SOFTWARE_ENDSTOPS
  #define MAX_SOFTWARE_ENDSTOP_X
  #define MAX_SOFTWARE_ENDSTOP_Y
  #define MAX_SOFTWARE_ENDSTOP_Z
#define HOMING_FEEDRATE_XY (50*60)
#define HOMING_FEEDRATE_Z  (4*60)
#define VALIDATE_HOMING_ENDSTOPS
#define EEPROM_SETTINGS     // Persistent storage with M500 and M501
#define EEPROM_CHITCHAT       // Give feedback on EEPROM commands. Disable to save PROGMEM.
#define HOST_KEEPALIVE_FEATURE        // Disable this if your host doesn't like keepalive messages
#define DEFAULT_KEEPALIVE_INTERVAL 2  // Number of seconds between "busy" messages. Set with M113.
#define BUSY_WHILE_HEATING            // Some hosts require "busy" messages even during heating
#define PREHEAT_1_LABEL       "PLA"
#define PREHEAT_1_TEMP_HOTEND 205
#define PREHEAT_1_TEMP_BED     60
#define PREHEAT_1_FAN_SPEED     0 // Value from 0 to 255
#define PREHEAT_2_LABEL       "PET"
#define PREHEAT_2_TEMP_HOTEND 260
#define PREHEAT_2_TEMP_BED    70
#define PREHEAT_2_FAN_SPEED     0 // Value from 0 to 255
#define PRINTJOB_TIMER_AUTOSTART
#define LCD_LANGUAGE en
#define DISPLAY_CHARSET_HD44780 JAPANESE
#define LCD_INFO_SCREEN_STYLE 0
#define SDSUPPORT
#define FYSETC_MINI_12864_2_0  // Type A/B. Discreet RGB Backlight
#define SOFT_PWM_SCALE 0
#define RGB_LED
  #define RGB_LED_R_PIN PB0
  #define RGB_LED_G_PIN PB6
  #define RGB_LED_B_PIN PB7
  #define RGB_LED_W_PIN -1
  #define PRINTER_EVENT_LEDS
#define SERVO_DELAY { 300 }
#define SD_RELOAD_SETTINGS

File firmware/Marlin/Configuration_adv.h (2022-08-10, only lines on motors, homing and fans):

#define E0_AUTO_FAN_PIN -1
#define E1_AUTO_FAN_PIN -1
#define E2_AUTO_FAN_PIN -1
#define E3_AUTO_FAN_PIN -1
#define E4_AUTO_FAN_PIN -1
#define E5_AUTO_FAN_PIN -1
#define CHAMBER_AUTO_FAN_PIN -1
#define X_HOME_BUMP_MM 5
#define Y_HOME_BUMP_MM 5
#define Z_HOME_BUMP_MM 2
#define HOMING_BUMP_DIVISOR { 2, 2, 4 }  // Re-Bump Speed Divisor (Divides the Homing Feedrate)
#define MICROSTEP_MODES { 16, 16, 16, 16, 16, 16 } // [1,2,4,8,16]
#define DIGIPOT_I2C_MOTOR_CURRENTS { 1.0, 1.0, 1.0, 1.0, 1.0, 1.0, 1.0, 1.0 }  //  AZTEEG_X3_PRO
    #define X_CURRENT     600  // (mA) RMS current. Multiply by 1.414 for peak current.
    #define X_MICROSTEPS   16  // 0..256
    #define Y_CURRENT     600
    #define Y_MICROSTEPS   16
    #define Z_CURRENT     600
    #define Z_MICROSTEPS   16
    #define E0_CURRENT    650
    #define E0_MICROSTEPS  16
    #define CURRENT_STEP_DOWN     50  // [mA]
    #define REPORT_CURRENT_CHANGE
  #define X_HYBRID_THRESHOLD     100  // [mm/s]
  #define X2_HYBRID_THRESHOLD    100
  #define Y_HYBRID_THRESHOLD     100
  #define Y2_HYBRID_THRESHOLD    100
  #define Z_HYBRID_THRESHOLD       3
  #define Z2_HYBRID_THRESHOLD      3
  #define Z3_HYBRID_THRESHOLD      3
  #define E0_HYBRID_THRESHOLD     30
  #define E1_HYBRID_THRESHOLD     30
  #define E2_HYBRID_THRESHOLD     30
  #define E3_HYBRID_THRESHOLD     30
  #define E4_HYBRID_THRESHOLD     30
  #define E5_HYBRID_THRESHOLD     30

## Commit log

2022-08-09 Update BOM.md
    Fixed AliExpress Links from de to www
2022-08-09 reformat BOM so it's more of a list to check off (#6)
    * reformat BOM so it's more of a list to check off
    * fix indentation
    * fix indentation
    * add checkboxes to BOM
    * add checkboxes to BOM
    * add checkboxes to BOM
    * grammar fix
    * little details to fix, consistent markdown formatting
2022-08-10 Updated BOM.md
    ...for missing parts. Still pulleys and idlers missing, as i need the exact size, and im not near my printer the next 10h.
2022-08-10 Updated BOM.md
    ...with newest changes because of pulley and idler.
2022-08-13 Updated BOM.md
    ...with the missing coupler for Z
2022-08-13 Add all 3D printed Parts
    ... as 3mf, as that is the superior file format, and what we should use. (and because its readable by like any slicer out there)
    [Endstopmount Y.3mf, Endstopwheel Z.3mf, Frontmount L v2.3mf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]
2022-08-13 move Marlin configs into subfolder to allow for future addition of other firmware configurations (#11)
    [Configuration.h, Configuration_adv.h]
2022-08-13 Updated BOM.md
    ...to add the missing rubber feets
2023-08-29 Add files via upload
    Added new fanshroud and new XZ-joiner (tuned by AWESOMEka001)
    [XZ-joiner v3.3mf, fanshroud v5 normal.3mf]
2023-09-30 Update BOM.md
    Added Lenghts for the 4 300mm Extrusions you have to cut
2023-09-30 Delete 3mf/Frontmount L v2.3mf
    deleted old Frontmount L v2 for the new v3
    [Frontmount L v2.3mf]
2023-09-30 Add files via upload
    Added new Frontmount L v3 for the shorter 128mm front 1515 extrusion
    [Frontmount L v3.3mf]
2023-10-01 Add files via upload
    QOL Updates:
    - thicker parts for the Endstopmounts on the XZ-joiner v4
    - Screwhead on X-Tensioner v3 is now flush sunk into it
    - the same now account fors the Endstopwheel Z v2
    [Endstopwheel Z v2.3mf, X-Tensioner v3.3mf, XZ-joiner v4.3mf]
2023-10-07 Update BOM.md
    A Set with M3 in 40mm was missing.
2023-10-07 Update README.md
    Uploaded the newest Ver 7 of Stable with Cheese (AIO II - Marlin Version) as step-file. Deleted f3d and old step.
2023-10-07 Update README.md
    Added a heated inserts version of the Fusion 360 web view, where you can watch all positions for the inserts.
2023-10-07 Update BOM.md (#17)
    - updated for using Klipper with AIO II, or using Klipper without AIO II but adding an BTT SKR Pico
2023-10-07 Add files via upload
    - if you want to add Klipper or Octoprint capabilities by adding a pi zero, pi zero w, pi zero 2 or pi zero 2 W, you simply need to print the "Pi Zero W mount..."
    - if you want to add Klipper with the SKR Pico, and scrap that AIO II, you can do that by now printing the "SKR Pico Mount Left" and "... Right"
    [Pi Zero W mount AIO II and SKR Pico.3mf, SKR Pico Mount Left.3mf, SKR Pico Mount Right.3mf]
2023-10-08 Add files via upload
    Added a manual variant of klicky-probe. All printable parts are done, you need all parts with "manualklicky" in front, which are exactly 3.
    Not tested yet, no tips on adding that to marlin or klipper yet.
    [manualklicky-hotendfan+partcoolingassembly v3.3mf, manualklicky-main.3mf, manualklicky-mount.3mf]
2023-10-14 Add files via upload
    added a tool mount, which just needs a 6x2mm neodym magnet, and then you can put a nozzle spanner (for example from twotrees) and a 2.5mm allen key, which is what basically all you need for all of fl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
    [tools_mount.3mf]
2024-01-18 Update BOM.md
    Since there was a report of a dodgy behaviour of one supplier, i changed that supplier
2026-01-26 Revise README with updated design file links
    Updated links to Fusion 360 design files and clarified version information. Adjusted text for better readability and accuracy regarding heated inserts.

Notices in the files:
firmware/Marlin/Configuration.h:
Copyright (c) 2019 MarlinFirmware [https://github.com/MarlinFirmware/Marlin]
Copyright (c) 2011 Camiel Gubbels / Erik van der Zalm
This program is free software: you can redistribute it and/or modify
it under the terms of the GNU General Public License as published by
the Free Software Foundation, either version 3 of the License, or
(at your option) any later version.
